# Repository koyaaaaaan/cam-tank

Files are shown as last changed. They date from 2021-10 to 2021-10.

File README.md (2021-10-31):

日本語話者のかたには [README.ja.md](/README.ja.md) を用意してあります。  
If you are Japanese speaker, we have [README.ja.md](/README.ja.md) for you.

# Cam Tank
Cam tank is Wifi control tank with camera streaming.

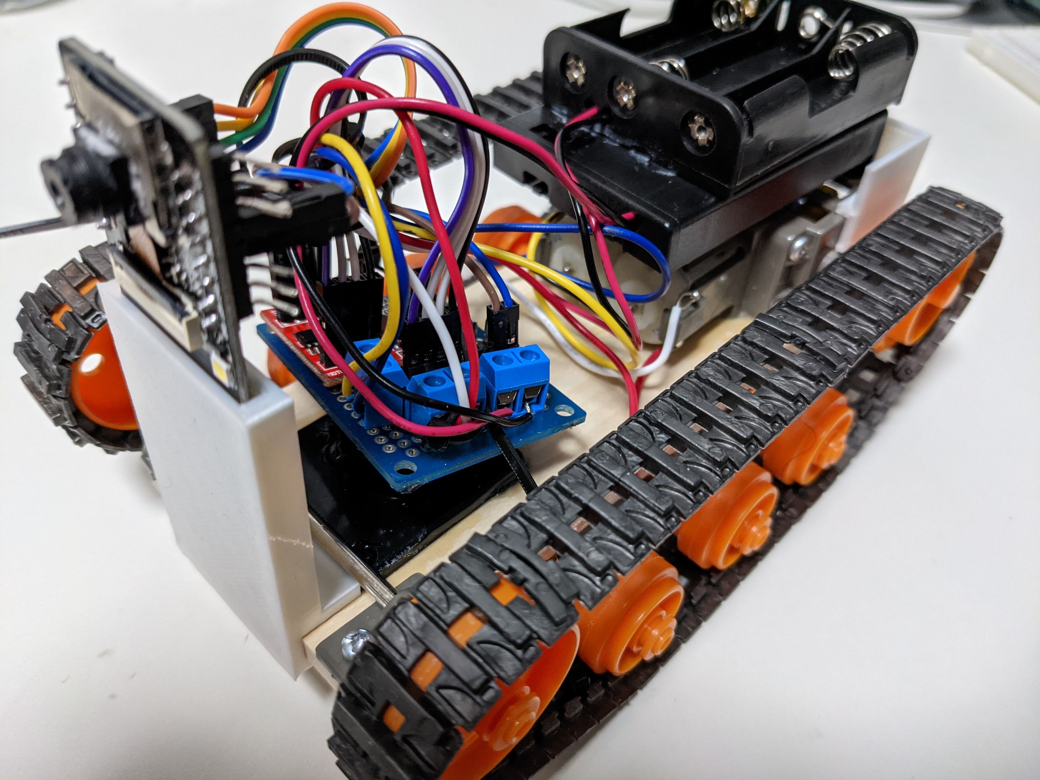
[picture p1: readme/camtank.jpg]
  
  
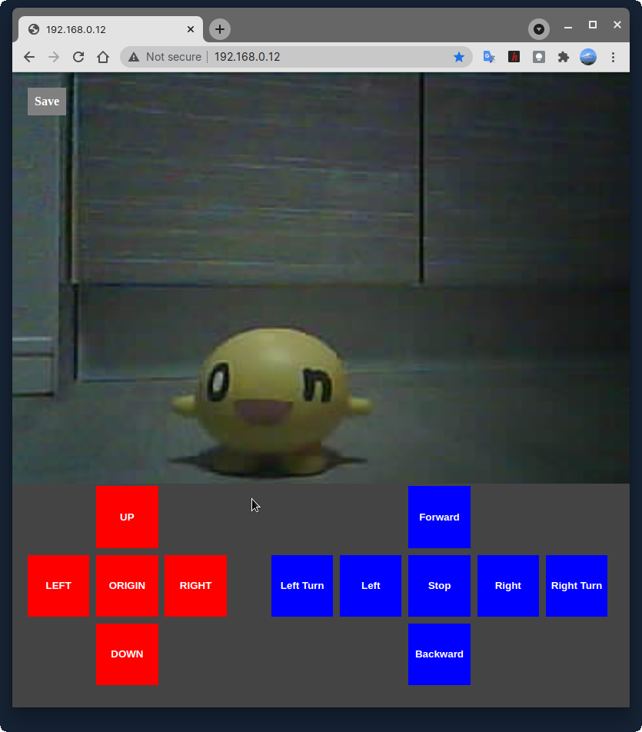
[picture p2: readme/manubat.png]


# Assemble

## Components
This project need to components below.

* ESP32-CAM
* TANK Kit with Dual Motor
* 2ch Motor Driver 
* Battery x 2 
* Servo Motor x 2 (Optional but... I don't recommend.)
* Cam Servo Mount (Optional but... I don't recommend.)

ESP32<br />
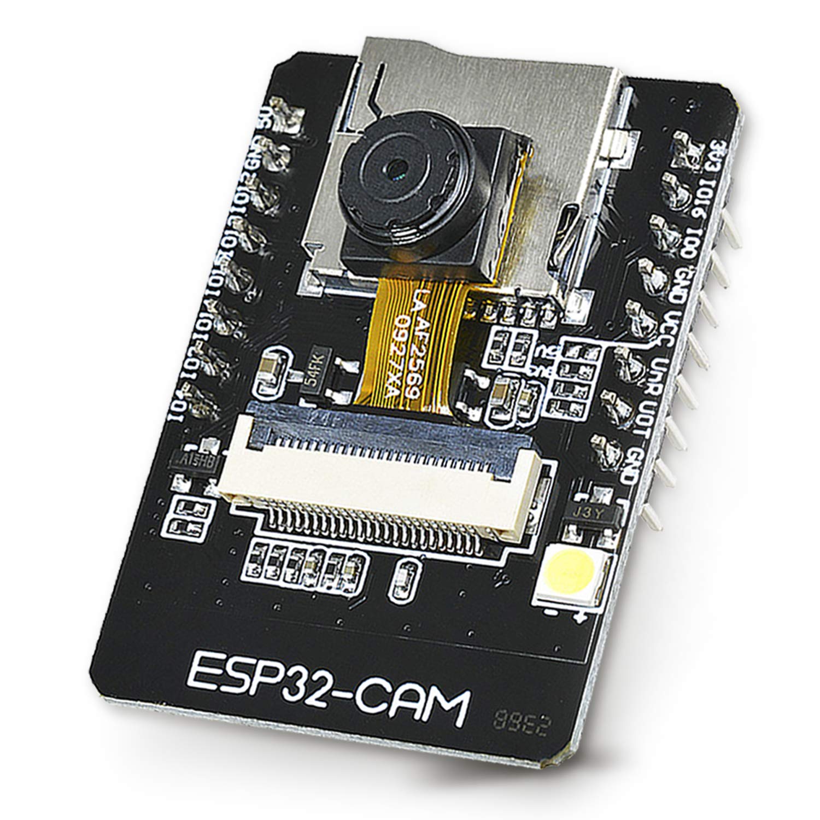
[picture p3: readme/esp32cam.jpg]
<br />
TANK Kit <br />
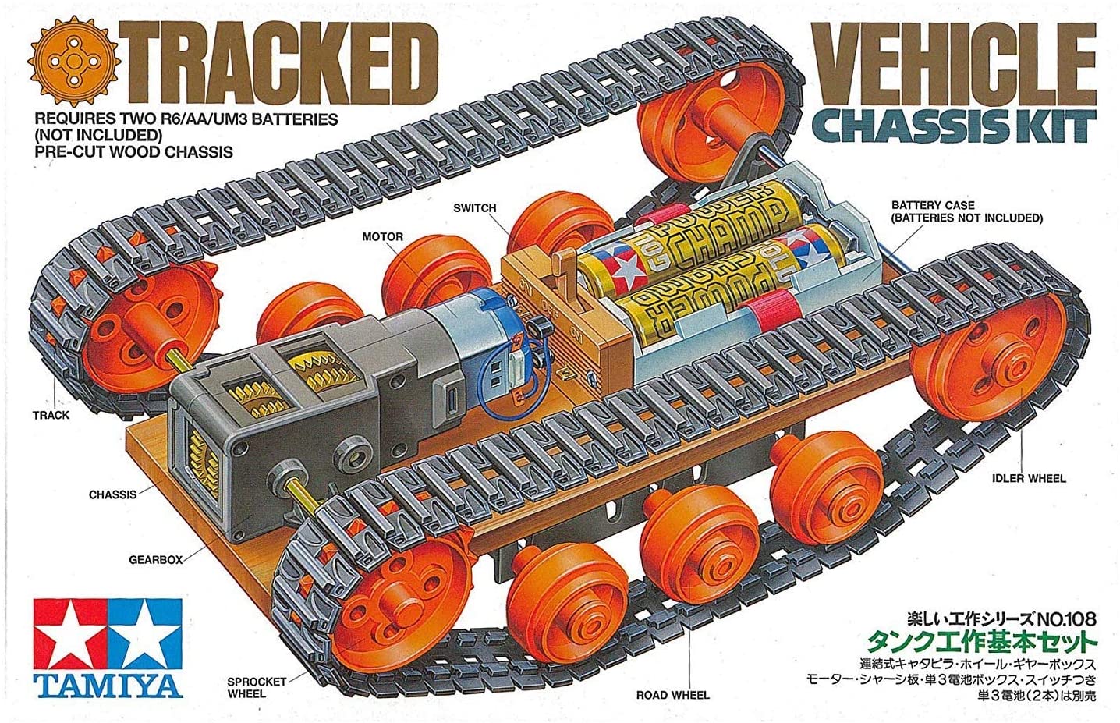
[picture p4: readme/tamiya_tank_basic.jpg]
<br />
Dual Motor<br />
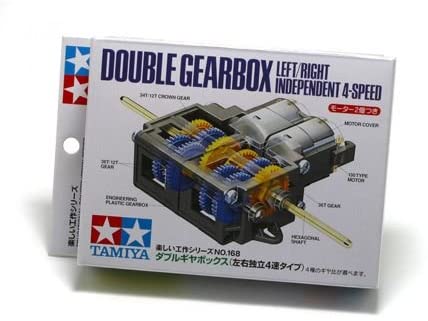
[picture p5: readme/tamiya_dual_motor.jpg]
<br />
Motor Driver<br />
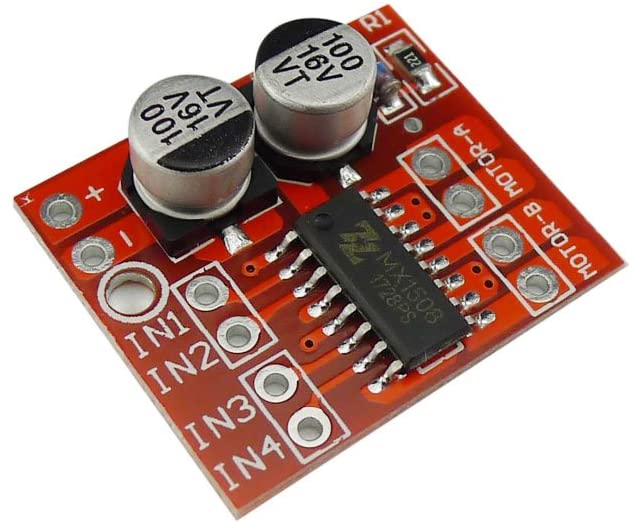
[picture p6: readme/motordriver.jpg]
<br />
Cam Servo Mount <br />
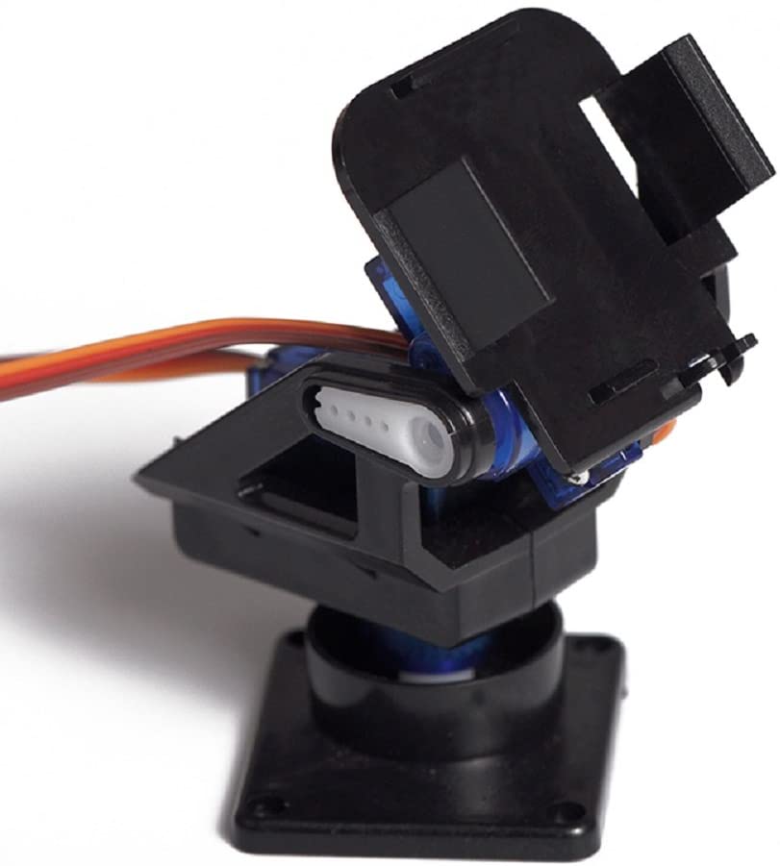
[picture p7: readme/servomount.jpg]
<br />

## ESP32 SetUP
### Install Source Code
1. Clone Git Project in your PC.<br />
Exec git clone command to download souce code in your pc.<br />
`git clone https://github.com/koyaaaaaan/cam-tank`<br />
<br />
<br />

2. Connect ESP32 and PC with Serial.<br />
In case of use USB Serial, connect like this.  
  
Connect each row.  <br />
| USB Serial | ESP32 CAM |
| --- | --- |
| 5V | 5V |
| RX | UoT |
| TX | UoR | 
| GND | GND |  

ESP32 Self Connection (This is for Installing the program) <br />
Connect each row.  <br />
| ESP32 CAM | ESP32 CAM |
| --- | --- |
| IO 0 (ZERO) | GND |
<br />
Actual circuit is like this.<br />
(When you run the program after uploading, unplug between IO0 and GND)<br />
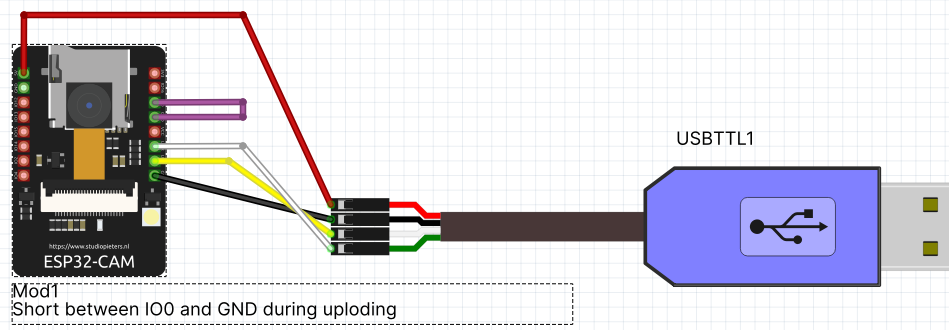
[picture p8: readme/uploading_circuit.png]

<br />
<br />

3. Open Source Code with Arduino IDE<br />
Open camtank.ino file.<br />
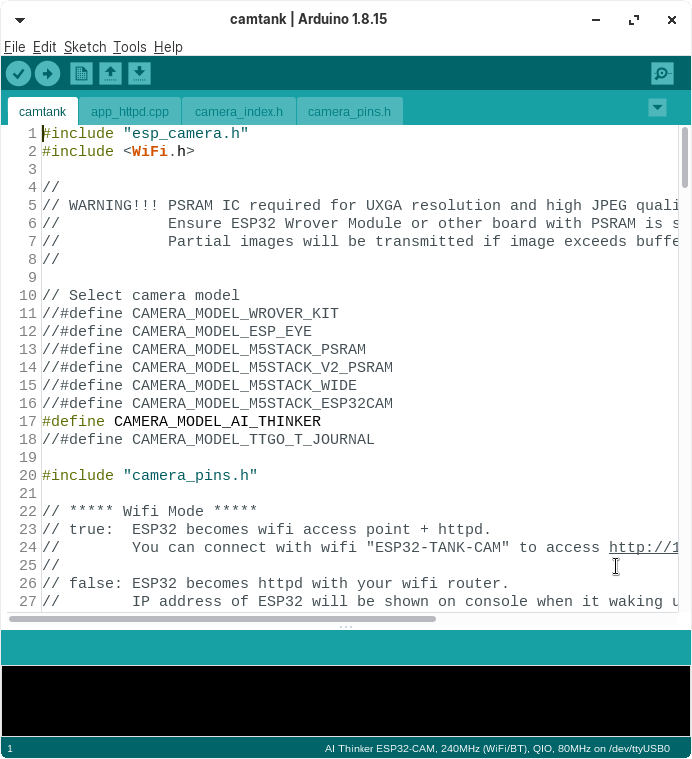
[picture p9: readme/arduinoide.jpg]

<br />
<br />

4. Compile and Install<br />
Do "Upload" command on Arduino IDE.<br /> 
When you see "Connecting..." in executing console, you may need to push reset button on ESP32-CAM to start installing.
<br />
<br />

5. Finish  
Remove the connection between GND and IO0(ZERO).
<br />
<br />
<br />

## Overview of Circuit

Here is a image after finished implementation.<br />
Details of "DC Motor" and "Servo" are below.<br />
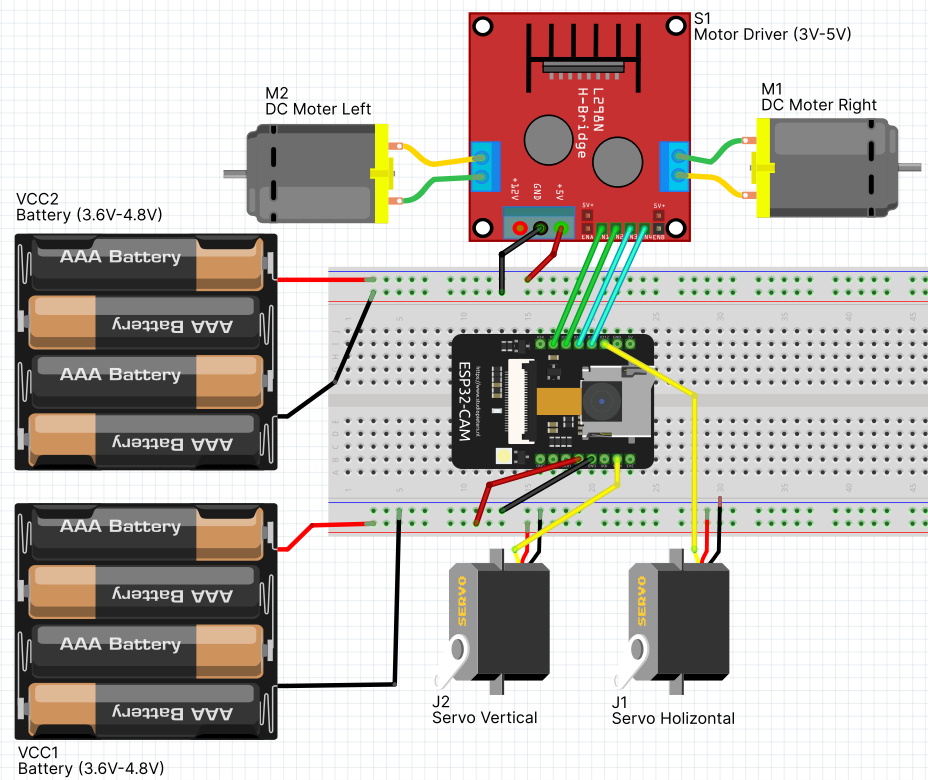
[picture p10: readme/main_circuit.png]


## DC Motor Circuit Implements
### Electric Circuit
Make circuit like this.  
*Note: Motor Driver may be diffirent behavior. Then please change connection.*
  
Connect each row.
| ESP32 CAM | Motor Driver | Battery | Motor | 
| --- | --- | --- | --- |
| IO2 | INT1 (MotorA Forward)  | | | 
| IO14 | INT2 (MotorA Backward) | | | 
| IO15 | INT3 (MotorB Forward)  | | | 
| IO13 | INT4 (MotorB Backward) | | | 
| | MororA 1 | | MotorA Positive | 
| | MororA 2 | | MotorA Negative | 
| | MororB 1 | | MotorB Positive | 
| | MororB 1 | | MotorB Negative | 
| | Positive | Positive (3-5V) | | 
| | Negative | Negative | | 
<br />
<br />
<br />

## Servo Circuit Implements (not Recommended)
*Warning: Camera of My ESP32-CAM didn't work with Servo PWM outputting. I guess its noise causes confusing camera behaviour. So I recommend to make test the circuit with breadboard before you make the circuit fixed.*

### Electric Circuit
Connect each row.
| ESP32 CAM | Servo Base (Horizontal) | Servo Cam (Vertical) | Battery | 
| --- | --- | --- | --- |
| IO 12 | PWM Controll | | | 
| | VCC | | Positive (5V) | 
| | GND | | Negative | 
| IO 16 | | PWM Controll | | 
| | | VCC | Positive (5V) | 
| | | GND | Negative | 

### Source code Modifying
You can find "# Servo" in camtank.ino and app_httpd.ccp.  
Please remove the comment outs around that.  
After do it, please install source code into ESP32 again.  
<br />
<br />
<br />

## Testing
1. Turn TANK CAM on.
2. Connecting the Wifi AP "ESP32-TANK-CAM" with password "tankcam".
3. Access http://192.168.0.12/ with Webbrowser.
4. You can see Controll Buttons and Cam Streaming.  
  
  
* Save Button -> Download Cam Screen as JPG format.  
* RED Buttons -> Controll Servo.  
* Blue Buttons - > Conrtoll Motors.  
<br />
<br />
<br />

## Hints
* Recommend to connect different battery sources ESP32 and Motors.  
Because energy drain by Motors is so much to restart ESP32 due to lack of Electricity when you connect only one bettery source.
* If you implement Servo, please give up it if Cam or Wifi was freezing when servo working.  
There can be some conflicting between cam and wifi and servo.  
Servo work(PWM) is a biggest issue.
* When you learn the system, you should use another components if you wanna implements more stable one.

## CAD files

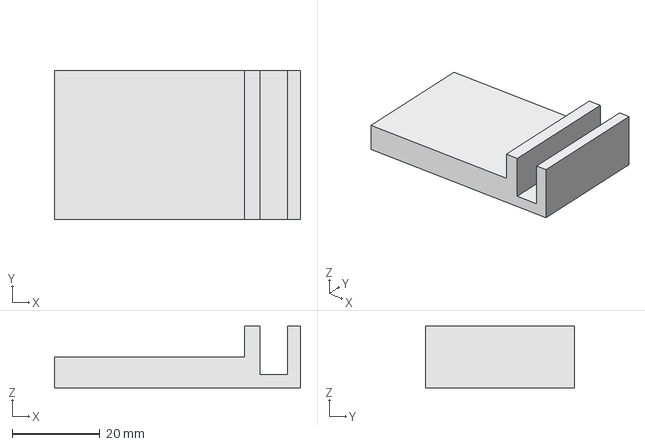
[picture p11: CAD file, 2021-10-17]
cad/camsocket.FCStd
56.0 x 34.0 x 14.0 mm

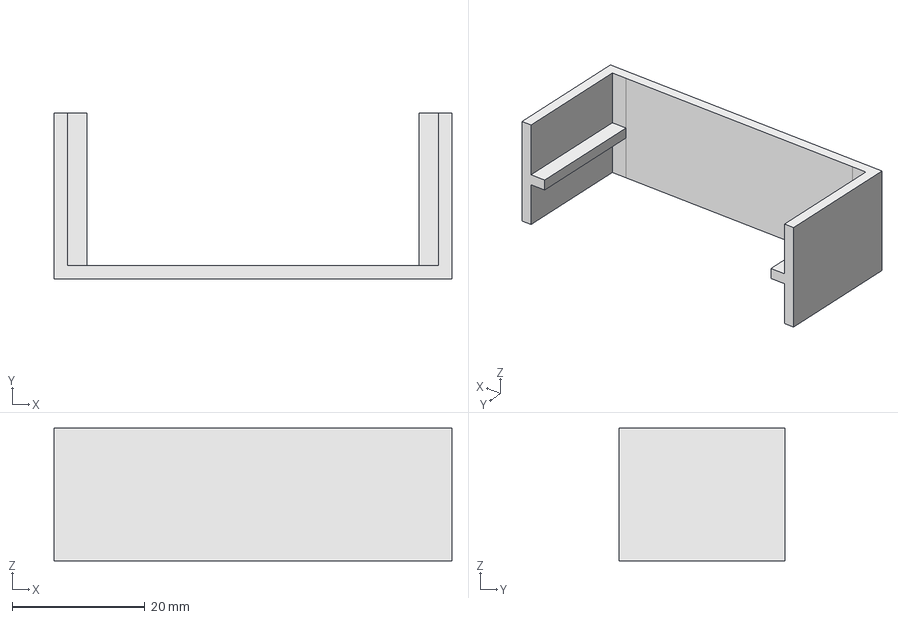
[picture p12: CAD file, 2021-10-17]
cad/btryguard.FCStd
60.0 x 25.0 x 20.0 mm

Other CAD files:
cad/camsocket-Body.stl
cad/btryguard-Body.stl

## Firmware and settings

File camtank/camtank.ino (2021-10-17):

#include "esp_camera.h"
#include <WiFi.h>

//
// WARNING!!! PSRAM IC required for UXGA resolution and high JPEG quality
//            Ensure ESP32 Wrover Module or other board with PSRAM is selected
//            Partial images will be transmitted if image exceeds buffer size
//

// Select camera model
//#define CAMERA_MODEL_WROVER_KIT
//#define CAMERA_MODEL_ESP_EYE
//#define CAMERA_MODEL_M5STACK_PSRAM
//#define CAMERA_MODEL_M5STACK_V2_PSRAM
//#define CAMERA_MODEL_M5STACK_WIDE
//#define CAMERA_MODEL_M5STACK_ESP32CAM
#define CAMERA_MODEL_AI_THINKER
//#define CAMERA_MODEL_TTGO_T_JOURNAL

#include "camera_pins.h"

// ***** Wifi Mode *****
// true:  ESP32 becomes wifi access point + httpd. 
//        You can connect with wifi "ESP32-TANK-CAM" to access http://192.168.0.12/ (default pass is tankcam).
//
// false: ESP32 becomes httpd with your wifi router. 
//        IP address of ESP32 will be shown on console when it waking up to access it http://xxxxxxxxxx/ .
const bool WifiMode = true; 

// ***** Configure for WifiMode = true *****
const char s_ssid[] = "ESP32-TANK-CAM";
const char s_pass[] = "tankcam";
const IPAddress s_ip(192,168,0,12);
const IPAddress s_subnet(255,255,255,0);

// ***** Configure for WifiMode = false *****
const char* c_ssid = "please put your wifi SSID here";
const char* c_pass = "please put your wifi PASS here";

// PIN SETTING
const int PIN_MOTOR_A_FW = 2;
const int PIN_MOTOR_A_BW = 14;
const int PIN_MOTOR_B_FW = 15;
const int PIN_MOTOR_B_BW = 13;
const int PIN_LED = 4;

// # If you wanna implement Camera XY Control System with Servo
// # Please remove comment out at "# Servo" (4 in camtank.ino, 1 in app_httpd.cpp).
// # But please note that PWM output noise can cause camera shut down.
// const int SERVO_BASE = 12; // # Servo
// const int SERVO_CAM = 16;  // # Servo

// void setServo(int sv1, int sv2); // # Servo
void startCameraServer();

void setup() {
  Serial.begin(115200);
  Serial.println();
  
  Serial.println("Set Up Cam...");
  cameraSetUp();
  
  Serial.println("Set Up User Pins...");
  pinSetting();  

  Serial.println("Starting HTTP Server...");
  if(WifiMode){
    startSoftWareAP();
  }else{
    startWifiConnection();
  }

  setUpComplete();
  Serial.println("Set Up Completed.");
}



void cameraSetUp(){
  camera_config_t config;
  config.ledc_channel = LEDC_CHANNEL_0;
  config.ledc_timer = LEDC_TIMER_0;
  config.pin_d0 = Y2_GPIO_NUM;
  config.pin_d1 = Y3_GPIO_NUM;
  config.pin_d2 = Y4_GPIO_NUM;
  config.pin_d3 = Y5_GPIO_NUM;
  config.pin_d4 = Y6_GPIO_NUM;
  config.pin_d5 = Y7_GPIO_NUM;
  config.pin_d6 = Y8_GPIO_NUM;
  config.pin_d7 = Y9_GPIO_NUM;
  config.pin_xclk = XCLK_GPIO_NUM;
  config.pin_pclk = PCLK_GPIO_NUM;
  config.pin_vsync = VSYNC_GPIO_NUM;
  config.pin_href = HREF_GPIO_NUM;
  config.pin_sscb_sda = SIOD_GPIO_NUM;
  config.pin_sscb_scl = SIOC_GPIO_NUM;
  config.pin_pwdn = PWDN_GPIO_NUM;
  config.pin_reset = RESET_GPIO_NUM;
  config.xclk_freq_hz = 20000000;
  config.pixel_format = PIXFORMAT_JPEG;
  
  // if PSRAM IC present, init with UXGA resolution and higher JPEG quality
  //                      for larger pre-allocated frame buffer.
  if(psramFound()){
    config.frame_size = FRAMESIZE_UXGA;
    config.jpeg_quality = 10;
    config.fb_count = 2;
  } else {
    config.frame_size = FRAMESIZE_UXGA;
    config.jpeg_quality = 12;
    config.fb_count = 1;
  }

  // camera init
  esp_err_t err = esp_camera_init(&config);
  if (err != ESP_OK) {
    Serial.printf("Camera init failed with error 0x%x", err);
    return;
  }

  sensor_t * s = esp_camera_sensor_get();
  // initial sensors are flipped vertically and colors are a bit saturated
  if (s->id.PID == OV3660_PID) {
    s->set_vflip(s, 1); // flip it back
    s->set_brightness(s, 1); // up the brightness just a bit
    s->set_saturation(s, -2); // lower the saturation
  }else{
    s->set_brightness(s, 0.6);
  }
  // drop down frame size for higher initial frame rate
  s->set_framesize(s, FRAMESIZE_QVGA);
}

void startSoftWareAP(){
  WiFi.softAP(s_ssid,s_pass);
  delay(100);
  WiFi.softAPConfig(s_ip,s_ip,s_subnet);
  IPAddress myIP = WiFi.softAPIP();
  
  Serial.println("ESP32 SoftAP Mode start.");
  Serial.print("SSID:");
  Serial.println(s_ssid);

  startCameraServer();
  
  Serial.print("Camera Ready! Use 'http://");
  Serial.print(myIP);
  Serial.println("' to connect");
}

void startWifiConnection(){
  Serial.print("ESP32 Wifi Connection Mode start. (SSID)");
  Serial.println(c_ssid);
  WiFi.begin(c_ssid, c_pass);
  while (WiFi.status() != WL_CONNECTED) {
    delay(500);
    Serial.print(".");
  }
  Serial.println("");
  Serial.println("WiFi connected");
  
  startCameraServer();
  
  Serial.print("Camera Ready! Use 'http://");
  Serial.print(WiFi.localIP());
  Serial.println("' to connect");
}

void pinSetting(){
  // Please put your gpio assign here
  pinMode(PIN_MOTOR_A_FW, OUTPUT);
  pinMode(PIN_MOTOR_A_BW, OUTPUT);
  pinMode(PIN_MOTOR_B_FW, OUTPUT);
  pinMode(PIN_MOTOR_B_BW, OUTPUT);
  pinMode(PIN_LED, OUTPUT);

  digitalWrite(PIN_MOTOR_A_FW ,LOW);
  digitalWrite(PIN_MOTOR_A_BW ,LOW);
  digitalWrite(PIN_MOTOR_B_FW ,LOW);
  digitalWrite(PIN_MOTOR_B_BW ,LOW);
  
  // setServo(SERVO_BASE, SERVO_CAM); // # Servo
}

void setUpComplete(){
  // When Set up is completed, built in LED will blink 2 times here.
  digitalWrite(PIN_LED, HIGH);
  delay(50);
  digitalWrite(PIN_LED, LOW);
  delay(100);
  
  digitalWrite(PIN_LED, HIGH);
  delay(50);
  digitalWrite(PIN_LED, LOW);
  delay(100);
  
}

void loop() {
  // put your main code here, to run repeatedly:
  delay(10000000);
}

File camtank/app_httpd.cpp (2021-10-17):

// Copyright 2015-2016 Espressif Systems (Shanghai) PTE LTD
//
// Licensed under the Apache License, Version 2.0 (the "License");
// you may not use this file except in compliance with the License.
// You may obtain a copy of the License at
//
//     http://www.apache.org/licenses/LICENSE-2.0
//
// Unless required by applicable law or agreed to in writing, software
// distributed under the License is distributed on an "AS IS" BASIS,
// WITHOUT WARRANTIES OR CONDITIONS OF ANY KIND, either express or implied.
// See the License for the specific language governing permissions and
// limitations under the License.
#include "esp_http_server.h"
#include "esp_timer.h"
#include "esp_camera.h"
#include "img_converters.h"
#include "fb_gfx.h"
#include "driver/ledc.h"
#include "sdkconfig.h"
#include "camera_index.h"
#include <Arduino.h>
#include <Servo.h>

#if defined(ARDUINO_ARCH_ESP32) && defined(CONFIG_ARDUHAL_ESP_LOG)
#include "esp32-hal-log.h"
#define TAG ""
#else
#include "esp_log.h"
static const char *TAG = "camera_httpd";
#endif

#if CONFIG_ESP_FACE_DETECT_ENABLED

#include "fd_forward.h"

#if CONFIG_ESP_FACE_RECOGNITION_ENABLED
#include "fr_forward.h"

#define ENROLL_CONFIRM_TIMES 5
#define FACE_ID_SAVE_NUMBER 7
#endif

#define FACE_COLOR_WHITE 0x00FFFFFF
#define FACE_COLOR_BLACK 0x00000000
#define FACE_COLOR_RED 0x000000FF
#define FACE_COLOR_GREEN 0x0000FF00
#define FACE_COLOR_BLUE 0x00FF0000
#define FACE_COLOR_YELLOW (FACE_COLOR_RED | FACE_COLOR_GREEN)
#define FACE_COLOR_CYAN (FACE_COLOR_BLUE | FACE_COLOR_GREEN)
#define FACE_COLOR_PURPLE (FACE_COLOR_BLUE | FACE_COLOR_RED)
#endif

#ifdef CONFIG_LED_ILLUMINATOR_ENABLED
int led_duty = 0;
bool isStreaming = false;
#ifdef CONFIG_LED_LEDC_LOW_SPEED_MODE
#define CONFIG_LED_LEDC_SPEED_MODE LEDC_LOW_SPEED_MODE
#else
#define CONFIG_LED_LEDC_SPEED_MODE LEDC_HIGH_SPEED_MODE
#endif
#endif

typedef struct
{
    httpd_req_t *req;
    size_t len;
} jpg_chunking_t;

#define PART_BOUNDARY "123456789000000000000987654321"
static const char *_STREAM_CONTENT_TYPE = "multipart/x-mixed-replace;boundary=" PART_BOUNDARY;
static const char *_STREAM_BOUNDARY = "\r\n--" PART_BOUNDARY "\r\n";
static const char *_STREAM_PART = "Content-Type: image/jpeg\r\nContent-Length: %u\r\nX-Timestamp: %d.%06d\r\n\r\n";

httpd_handle_t stream_httpd = NULL;
httpd_handle_t camera_httpd = NULL;

#if CONFIG_ESP_FACE_DETECT_ENABLED

static int8_t detection_enabled = 0;

static mtmn_config_t mtmn_config = {0};

#if CONFIG_ESP_FACE_RECOGNITION_ENABLED
static int8_t recognition_enabled = 0;
static int8_t is_enrolling = 0;
static face_id_list id_list = {0};
#endif

#endif

Servo svBASE;
Servo svCAM;

typedef struct
{
    size_t size;  //number of values used for filtering
    size_t index; //current value index
    size_t count; //value count
    int sum;
    int *values; //array to be filled with values
} ra_filter_t;

static ra_filter_t ra_filter;

static ra_filter_t *ra_filter_init(ra_filter_t *filter, size_t sample_size)
{
    memset(filter, 0, sizeof(ra_filter_t));

    filter->values = (int *)malloc(sample_size * sizeof(int));
    if (!filter->values)
    {
        return NULL;
    }
    memset(filter->values, 0, sample_size * sizeof(int));

    filter->size = sample_size;
    return filter;
}

static int ra_filter_run(ra_filter_t *filter, int value)
{
    if (!filter->values)
    {
        return value;
    }
    filter->sum -= filter->values[filter->index];
    filter->values[filter->index] = value;
    filter->sum += filter->values[filter->index];
    filter->index++;
    filter->index = filter->index % filter->size;
    if (filter->count < filter->size)
    {
        filter->count++;
    }
    return filter->sum / filter->count;
}

#if CONFIG_ESP_FACE_DETECT_ENABLED
#if CONFIG_ESP_FACE_RECOGNITION_ENABLED
static void rgb_print(dl_matrix3du_t *image_matrix, uint32_t color, const char *str)
{
    fb_data_t fb;
    fb.width = image_matrix->w;
    fb.height = image_matrix->h;
    fb.data = image_matrix->item;
    fb.bytes_per_pixel = 3;
    fb.format = FB_BGR888;
    fb_gfx_print(&fb, (fb.width - (strlen(str) * 14)) / 2, 10, color, str);
}

static int rgb_printf(dl_matrix3du_t *image_matrix, uint32_t color, const char *format, ...)
{
    char loc_buf[64];
    char *temp = loc_buf;
    int len;
    va_list arg;
    va_list copy;
    va_start(arg, format);
    va_copy(copy, arg);
    len = vsnprintf(loc_buf, sizeof(loc_buf), format, arg);
    va_end(copy);
    if (len >= sizeof(loc_buf))
    {
        temp = (char *)malloc(len + 1);
        if (temp == NULL)
        {
            return 0;
        }
    }
    vsnprintf(temp, len + 1, format, arg);
    va_end(arg);
    rgb_print(image_matrix, color, temp);
    if (len > 64)
    {
        free(temp);
    }
    return len;
}
#endif
static void draw_face_boxes(dl_matrix3du_t *image_matrix, box_array_t *boxes, int face_id)
{
    int x, y, w, h, i;
    uint32_t color = FACE_COLOR_YELLOW;
    if (face_id < 0)
    {
        color = FACE_COLOR_RED;
    }
    else if (face_id > 0)
    {
        color = FACE_COLOR_GREEN;
    }
    fb_data_t fb;
    fb.width = image_matrix->w;
    fb.height = image_matrix->h;
    fb.data = image_matrix->item;
    fb.bytes_per_pixel = 3;
    fb.format = FB_BGR888;
    for (i = 0; i < boxes->len; i++)
    {
        // rectangle box
        x = (int)boxes->box[i].box_p[0];
        y = (int)boxes->box[i].box_p[1];
        w = (int)boxes->box[i].box_p[2] - x + 1;
        h = (int)boxes->box[i].box_p[3] - y + 1;
        fb_gfx_drawFastHLine(&fb, x, y, w, color);
        fb_gfx_drawFastHLine(&fb, x, y + h - 1, w, color);
        fb_gfx_drawFastVLine(&fb, x, y, h, color);
        fb_gfx_drawFastVLine(&fb, x + w - 1, y, h, color);
#if 0
        // landmark
        int x0, y0, j;
        for (j = 0; j < 10; j+=2) {
            x0 = (int)boxes->landmark[i].landmark_p[j];
            y0 = (int)boxes->landmark[i].landmark_p[j+1];
            fb_gfx_fillRect(&fb, x0, y0, 3, 3, color);
        }
#endif
    }
}
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

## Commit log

2021-10-23 add fritzing
    [main_circuit.fzz, uploading_circuit.fzz]
2021-10-23 move readme resources
    [main_circuit.fzz, uploading_circuit.fzz]
2021-10-23 replace main png
    [main_circuit.fzz]
